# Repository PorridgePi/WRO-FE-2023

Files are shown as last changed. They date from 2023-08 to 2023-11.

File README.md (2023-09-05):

# WRO 2023 Future Engineers



# Team Information

Team ID: `FE0901`

Team Name: `raffles institution team 3`

Team Members
- [Yikun](https://github.com/PorridgePi)
- [Zachary](https://github.com/Zachareeeeee)

# Overview

Welcome to the GitHub repository for Team `FE0901` participating in WRO 2023. In this competition, we are building an autonomous robotic vehicle capable of completing 2 different challenges. This README provides a simple overview. If you wish to delve deeper into our engineering process, please check out our [Engineering Journal](docs/Engineering%20Journal.md) or [download it as PDF](https://github.com/PorridgePi/WRO-FE-2023/blob/main/docs/Engineering%20Journal.pdf).

## Demo

A demonstration video of our robot in action can be found on YouTube (or in the [video.md](video/video.md) file): [https://youtu.be/pbWbQL5pThI](https://youtu.be/pbWbQL5pThI)

Watch the video (https://www.youtube.com/embed/pbWbQL5pThI)

### Key Timestamps
Open Challenge
- Run 1: [00:03](https://youtu.be/pbWbQL5pThI&t=3)
- Runs 2 & 3: [01:15](https://youtu.be/pbWbQL5pThI&t=75)

Obstacle Challenge:
- Run 1: [03:40](https://youtu.be/pbWbQL5pThI&t=221)

# Usage
For Code, Using Visual Studio Code:
- Clone this repository: `git clone https://github.com/PorridgePi/WRO-FE-2023`
- Change directory: `cd ./WRO-FE-2023/`
- Initialise Git submodule(s): `git submodule update --init --recursive`
- Open the repository in VSCode: `code ./`
- Install the PlatformIO plugin
- Select the appropriate PlatformIO Environment
- Use the PlatformIO plugin to compile and upload code onto the microcontroller (Raspberry PI Pico)

For Camera (OpenMV): Using the [OpenMV IDE](https://openmv.io/pages/download)
- Open the camera code (`src/omv_main.py`) in OpenMV IDE
- Upload code onto OpenMV by:
    - Select `Tools` Menu
    - Click `Save open script onto OpenMV Cam (as main.py)`

For Documentation, Using [Obsidian](https://obsidian.md/):
- Clone this repository: `git clone https://github.com/PorridgePi/WRO-FE-2023`
- Open the cloned directory as a Vault

For PCB, Using [KiCAD](https://www.kicad.org/):
- Clone this repository: `git clone https://github.com/PorridgePi/WRO-FE-2023`
- Open the file `schemes/WRO_2023/WRO_2023.kicad_pro`

# Repository Content
- `.github/workflows/platformio-ci.yml`: GitHub Actions CI workflow for PlatformIO ([Documentation](https://docs.platformio.org/en/latest/integration/ci/github-actions.html))
- `.vscode/`: Folder containing VSCode workspace settings
    - `extensions.json`: List of recommended and unwanted extensions ([Documentation](https://code.visualstudio.com/docs/editor/extension-gallery#_workspace-recommended-extensions))
- `models/`: 3D models
- `others/`: Other files
- `schemes/`: Schematic diagram and PCB
    - `WRO_2023`: PCB files that can be opened in KiCAD
- `scripts/`: Scripts for PlatformIO
    - `ci.sh`: Script for CI test
- `src/`: Main code
    - `lib/`: Libraries for components
        - Notably:
            - `lib/private/Common.h`: Shared code between `open.cpp` and `obstacle.cpp`
            - `lib/Mecha_QMC5883L`: [Forked version](https://github.com/PorridgePi/Mecha_QMC5883L) of library for the QMC5883L magnetometer
    - `test/`: Test code
    - `main.cpp`: Placeholder file
    - `obstacle.cpp`: Code for the Obstacle Challenge
    - `open.cpp`: Code for the Open Challenge
- `t-photos`: Team photo
- `v-photos`: Photos of the vehicle (from many different angles!)
- `video`: Contains [video.md](video/video.md) with the link to the video of the driving demonstration
- `.clang-format`: ClangFormat code style file - to format code in VSCode
- `.gitignore`: gitignore file ([Documentation](https://git-scm.com/docs/gitignore))
- `platformio.ini`: PlatformIO configuration file ([Documentation](https://docs.platformio.org/en/stable/projectconf/index.html))
- `README.md`: This file

# Reminders before Running
1. Calibrate compass(es)
2. Ensure steering mechanism is tightened
3. Clean wheels to ensure grip

# Hardware used
- **Motor:** 1x GM25-12CPR 
- **Servo:** 1x MG996R
- **Motor Driver:** 1x AT8236
- **Microcontroller:** 1x Raspberry Pi Pico
- **Voltage Regulator (5V):** 1x CKCS-BK-2
- **LiDAR:** 5x TF-Luna
- **Camera:** 1x OpenMV M7
- **Compass:** 1x GY-273 and 1x GY-271
- **Battery:** 1x Turnigy nano-tech 1300mAh 3S 45~90C Lipo Pack

# Continual Integration (CI) Testing

We have a simple CI testing setup with GitHub Actions, using the `scripts/ci.sh` script to automate the process of building our code for all different environments in `platformio.ini`. It checks for build success and ensures that the code can be successfully compiled.

CI is a critical aspect of our development process. It allows us to detect issues and errors in our codebase as soon as they occur. This early detection is invaluable in preventing the accumulation of errors and simplifying debugging.

Besides, our project involves multiple team members working collaboratively. CI ensures that all code changes made by different team members do not introduce regressions or break existing functionality.

To check the status of our CI, go to the [`Actions` tab](https://github.com/PorridgePi/WRO-FE-2023/actions) and view the workflow runs. If everything is going well, you should be only seeing green ticks. However, if you are seeing red crosses, something is up, but don't fret, we are definitely working hard to iron out the bugs!

(or alternatively, just look at the badge below for the CI status)



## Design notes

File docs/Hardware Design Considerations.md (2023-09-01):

# Wheels
- Wide v.s. Thin
    - affect surface area in contact with ground, affecting how rubber gets squished
- Size (i.e. diameter) affects
    - size of cavity to allow steering
    - torque
        - larger the diameter, moment of inertia is higher, more torque required
    - distance travelled per revolution
- Mass

# Motor
- Encoder
- Motor Stall Current
    - proportional to Vin
- nominal voltage
- [Pulling power from the balance plug - RC Groups - https://www.rcgroups.com/forums/showthread.php?1442019-Pulling-power-from-the-balance-plug](https://www.rcgroups.com/forums/showthread.php?1442019-Pulling-power-from-the-balance-plug)
# Steering
- Take note of steer radius
    - tightest turn at corners would be less than 40cm (i.e. both blocks require keeping to the left)
    - movement between blocks would be around a maximum turn radius of 50cm
- Servo
    - [Servo - writeMicroseconds() - Arduino Reference - https://reference.arduino.cc/reference/en/libraries/servo/writemicroseconds/](https://reference.arduino.cc/reference/en/libraries/servo/writemicroseconds/)
    - use this instead of `.write()`
- [Servo Motors - Arduino - Wiki.nus - https://wiki.nus.edu.sg/display/Arduino/Servo+Motors](https://wiki.nus.edu.sg/display/Arduino/Servo+Motors)

    - need to take into account the length and width of the vehicle
    - lines from both front wheels and the line through back wheels should all come together at a single point
        - 
        - Tech Explained: Ackermann Steering Geometry - Racecar Engineering

- Website: [Ackerman Steering](http://datagenetics.com/blog/december12016/index.html)

# Ranging/Localisation
- LiDAR
- Camera
- Optical Flow

# Orientation
- IMU
- Compass

# Notes
- Ideally only camera for SLAM would yield the smallest robot

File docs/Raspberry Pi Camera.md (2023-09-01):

w- on [[2023-04-26]], checked out:
    - [Raspberry Pi and PiCam setup (headless)](https://gist.github.com/sageworksstudio/b0954d2d6cfac7d4a00e776953324a2c)
    - [Connect the Camera Module | Getting started with the Camera Module](https://projects.raspberrypi.org/en/projects/getting-started-with-picamera/2)
- [[2023-05-03]]
    - Issue:
        - `vcgencmd get_camera`: `supported=1 detected=1, libcamera interfaces=0`
        - but `libcamera-hello`: `ERROR: *** no cameras available ***`
    - Fix:
        - [Raspberry Pi Documentation - Camera software](https://www.raspberrypi.com/documentation/computers/camera_software.html)
            - > On Raspberry Pi 3 and earlier devices running Bullseye you need to re-enable Glamor in order to make the X-Windows hardware accelerated preview window work. To do this enter sudo raspi-config at a terminal window and then choose Advanced Options, Glamor and Yes. Finally quit raspi-config and let it reboot your Raspberry Pi.
            - > Raspberry Pi 3 and older devices may not by default be using the correct display driver. Refer to the /boot/config.txt file and ensure that either dtoverlay=vc4-fkms-v3d or dtoverlay=vc4-kms-v3d is currently active. Please reboot if you needed to change this.
        - Original reference to
            - [libcamera-apps not working on RPi 3 Model B+ · Issue #125 · raspberrypi/libcamera-apps](https://github.com/raspberrypi/libcamera-apps/issues/125)
            - [Raspbeery (bullseye) && libcamera - Stack Overflow](https://stackoverflow.com/questions/71709549/raspbeery-bullseye-libcamera/71712175#71712175)
    - Usage: `libcamera-hello -t 0` for no timeout
- [[2023-05-08]]
```python
from picamera2 import Picamera2
picam2 = Picamera2()
print(picam2.sensor_modes)
```

```json
[{'format': SRGGB10_CSI2P, 'unpacked': 'SRGGB10', 'bit_depth': 10, 'size': (640, 480), 'fps': 103.33, 'crop_limits': (1000, 752, 1280, 960), 'exposure_limits': (75, 11766829, None)}, {'format': SRGGB10_CSI2P, 'unpacked': 'SRGGB10', 'bit_depth': 10, 'size': (1640, 1232), 'fps': 41.85, 'crop_limits': (0, 0, 3280, 2464), 'exposure_limits': (75, 11766829, None)}, {'format': SRGGB10_CSI2P, 'unpacked': 'SRGGB10', 'bit_depth': 10, 'size': (1920, 1080), 'fps': 47.57, 'crop_limits': (680, 692, 1920, 1080), 'exposure_limits': (75, 11766829, None)}, {'format': SRGGB10_CSI2P, 'unpacked': 'SRGGB10', 'bit_depth': 10, 'size': (3280, 2464), 'fps': 21.19, 'crop_limits': (0, 0, 3280, 2464), 'exposure_limits': (75, 11766829, None)}, {'format': SRGGB8, 'unpacked': 'SRGGB8', 'bit_depth': 8, 'size': (640, 480), 'fps': 103.33, 'crop_limits': (1000, 752, 1280, 960), 'exposure_limits': (75, 11766829, None)}, {'format': SRGGB8, 'unpacked': 'SRGGB8', 'bit_depth': 8, 'size': (1640, 1232), 'fps': 41.85, 'crop_limits': (0, 0, 3280, 2464), 'exposure_limits': (75, 11766829, None)}, {'format': SRGGB8, 'unpacked': 'SRGGB8', 'bit_depth': 8, 'size': (1920, 1080), 'fps': 47.57, 'crop_limits': (680, 692, 1920, 1080), 'exposure_limits': (75, 11766829, None)}, {'format': SRGGB8, 'unpacked': 'SRGGB8', 'bit_depth': 8, 'size': (3280, 2464), 'fps': 21.19, 'crop_limits': (0, 0, 3280, 2464), 'exposure_limits': (75, 11766829, None)}]
>>> print(picam2.sensor_modes)
[{'format': SRGGB10_CSI2P, 'unpacked': 'SRGGB10', 'bit_depth': 10, 'size': (640, 480), 'fps': 103.33, 'crop_limits': (1000, 752, 1280, 960), 'exposure_limits': (75, 11766829, None)}, {'format': SRGGB10_CSI2P, 'unpacked': 'SRGGB10', 'bit_depth': 10, 'size': (1640, 1232), 'fps': 41.85, 'crop_limits': (0, 0, 3280, 2464), 'exposure_limits': (75, 11766829, None)}, {'format': SRGGB10_CSI2P, 'unpacked': 'SRGGB10', 'bit_depth': 10, 'size': (1920, 1080), 'fps': 47.57, 'crop_limits': (680, 692, 1920, 1080), 'exposure_limits': (75, 11766829, None)}, {'format': SRGGB10_CSI2P, 'unpacked': 'SRGGB10', 'bit_depth': 10, 'size': (3280, 2464), 'fps': 21.19, 'crop_limits': (0, 0, 3280, 2464), 'exposure_limits': (75, 11766829, None)}, {'format': SRGGB8, 'unpacked': 'SRGGB8', 'bit_depth': 8, 'size': (640, 480), 'fps': 103.33, 'crop_limits': (1000, 752, 1280, 960), 'exposure_limits': (75, 11766829, None)}, {'format': SRGGB8, 'unpacked': 'SRGGB8', 'bit_depth': 8, 'size': (1640, 1232), 'fps': 41.85, 'crop_limits': (0, 0, 3280, 2464), 'exposure_limits': (75, 11766829, None)}, {'format': SRGGB8, 'unpacked': 'SRGGB8', 'bit_depth': 8, 'size': (1920, 1080), 'fps': 47.57, 'crop_limits': (680, 692, 1920, 1080), 'exposure_limits': (75, 11766829, None)}, {'format': SRGGB8, 'unpacked': 'SRGGB8', 'bit_depth': 8, 'size': (3280, 2464), 'fps': 21.19, 'crop_limits': (0, 0, 3280, 2464), 'exposure_limits': (75, 11766829, None)}]
```

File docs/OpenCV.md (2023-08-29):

- [[2023-05-03]]
    - with [[Raspberry Pi Camera]]
        - Optimisation
            - [prepkg/opencv-raspberrypi: Precompiled OpenCV 4.7.0 binaries for Raspberry Pi 3 & 4](https://github.com/prepkg/opencv-raspberrypi)
            - [Optimizing OpenCV on the Raspberry Pi - PyImageSearch](https://pyimagesearch.com/2017/10/09/optimizing-opencv-on-the-raspberry-pi/)
        - [Using the Raspberry Pi Camera on Bullseye OS and OpenCV | Technology Tutorials](https://toptechboy.com/using-the-raspberry-pi-camera-on-bullseye-os-and-opencv/)
            - `pip install opencv-python==4.6.0.66`
            ```python
            import cv2
            from picamera2 import Picamera2
            picam2 = Picamera2()
            picam2.preview_configuration.main.size = (1280,720)
            picam2.preview_configuration.main.format = "RGB888"
            picam2.preview_configuration.align()
            picam2.configure("preview")
            picam2.start()
            while True:
                im= picam2.capture_array()
                cv2.imshow("Camera", im)
                if cv2.waitKey(1)==ord('q'):
                    break
            cv2.destroyAllWindows()
            ```

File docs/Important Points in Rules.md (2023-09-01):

# Focus Areas
- CV + sensor fusion
- open-source hardware
- movement different from differential drive
- optimal strategies
- engineering journal
# Getting Started Guide
- https://world-robot-olympiad-association.github.io/future-engineers-gs/
# Team's Own Work
- Note: 3.7 It is not allowed to use a vehicle’s control program that is (a.) the same or too similar to solutions sold online or (b.) the same or too similar to another solution at the competition and clearly not the own work of the team. This includes solutions from teams of the same institution and/or country. Since manufactured vehicles/sets can be used in the competition, the constructions of vehicles are not checked for plagiarism.
# Game Description
- One car per attempt will try to achieve the best time by driving several laps fully autonomously. The two challenges are the following:
    - Open Challenge: The vehicle must complete three (3) laps on the track with random placements of the inside track walls.
    - Obstacle Challenge: The vehicle must complete three (3) laps on the track with randomly placed green and red traffic signs. The traffic signs indicate the side of the lane the vehicle must follow. The traffic sign to keep to the right side of the lane is a red pillar. The traffic sign to keep to the left side of the lane is a green pillar. The continuation of the vehicle to the third round is indicated by the last traffic sign of the second round. A green traffic sign indicates that the robot must go ahead and continue the third round in the same direction. A red traffic sign indicates that the vehicle must turn around and complete the third round in the opposite direction. The vehicle is not allowed to move or knock down the traffic signs.

The starting direction in which the car must drive on the track (clockwise or counterclockwise) will vary in different challenge rounds. The starting position of the car as well as the number and location of traffic signs are randomly defined before the round (after the check time). The following graphic shows the game field with the game objects.

Straightforward Section
- 6 zones
- 4 T-intersections and 2 X-intersections
- traffic sign's seats
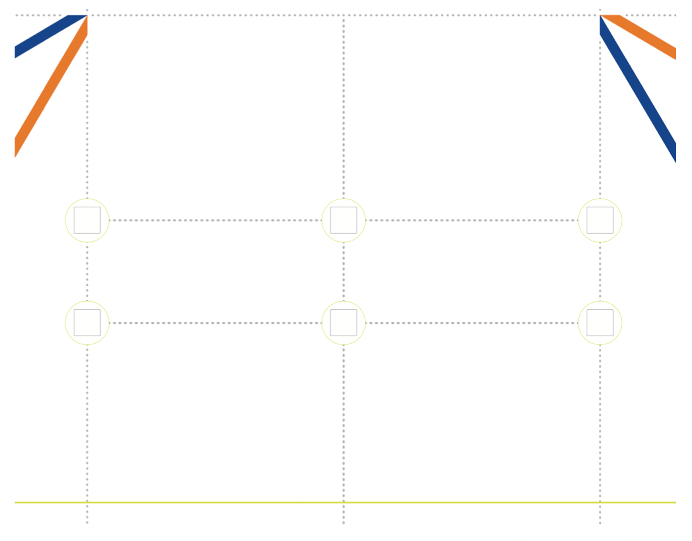
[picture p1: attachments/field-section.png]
    - 

# Engineer’s documentation on GitHub
documentation that presents their engineering progress, the final vehicle design and final vehicle source code

This documentation must be uploaded to the GitHub public repository, and a hardcopy must be submitted at the international final.

must provide the following:
-   Discussion, Information and motivation for the vehicle’s mobility, power and sense, and obstacle management.
    - sense - decision making
-   Photos of the vehicle (from every side, from top and bottom), and a team photo.
-   URL to YouTube (should be either public or accessible by link) showing the vehicle driving autonomously.
    - That part of the video where driving demonstration exists, must be at least 30 seconds in length.
    - One video for each challenge must be provided.
- Link to a GitHub public repository
    - with the code for all components which were programmed to participate in the competition
    - The repository may also include the files for models used by 3D printers, laser cutting machines and CNC machines to produce the vehicle elements.
    - The history of commits should contain at least 3 commits
        - the first one not later than 2 months before the competition – it must contain not less than 1/5 of the final amount of the code
        - The second one is not later than 1 month before the competition
        - the third one not later than 1 week before the competition.
    - The repository must contain a README.md file with a short description in English (not less than 5000 characters) of the designed solution.
    - The goal of the description is to clarify
        - which modules the code consists of
        - how they are related to the electromechanical components of the vehicle
        - and what is the process to build/compile/upload the code to the vehicle’s controllers
            - "Usage" section
    - A template for the GitHub repos is available on https://github.com/World-Robot-Olympiad-Association/wro2022-fe-template.

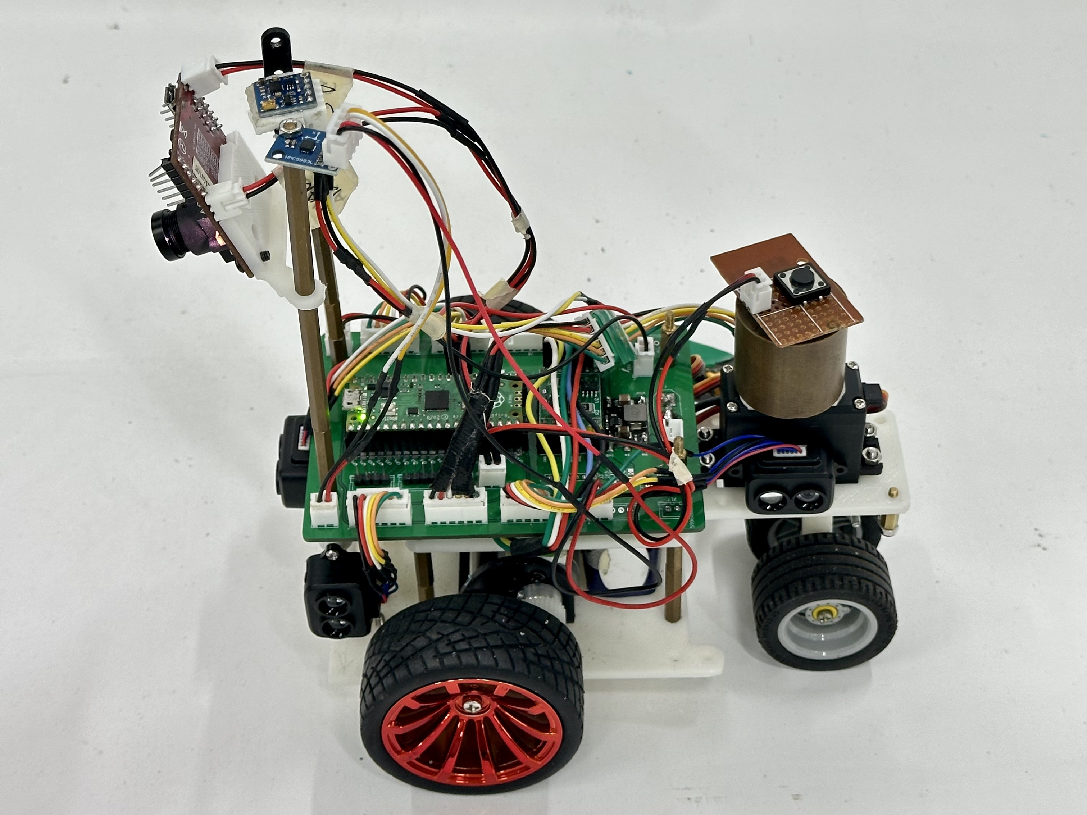
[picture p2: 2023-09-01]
v-photos/FE0901_Vehicle_Top_Left.jpeg

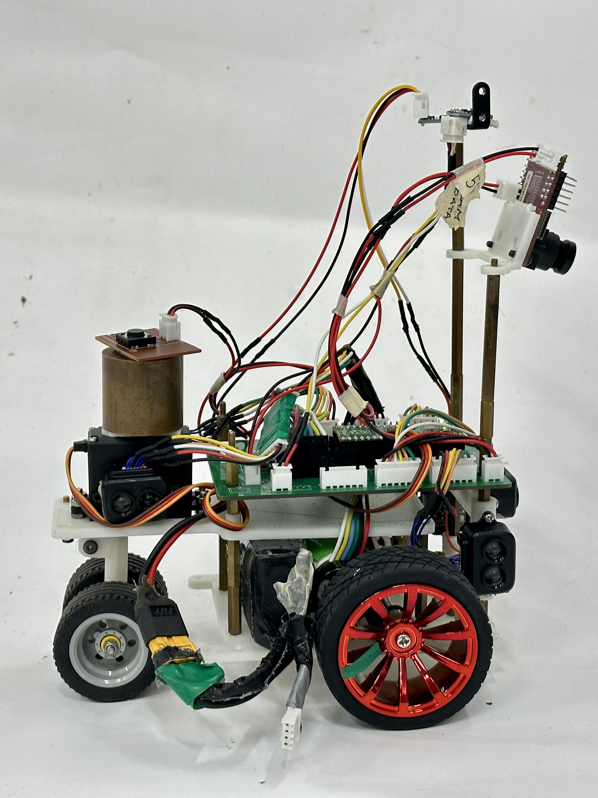
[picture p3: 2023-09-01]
v-photos/FE0901_Vehicle_Right.jpeg

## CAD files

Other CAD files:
models/bot.f3d

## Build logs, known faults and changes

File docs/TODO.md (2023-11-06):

- [ ] Things to pack
    - [ ] M3, M2 Screwsw
    - [x] Backup prints (especially steering column(
    - [ ] 3x TFLunas + Cables
    - [ ] 2x IMUs + Cables
    - [x] Spare Servo
    - [x] Spare Motor
    - [x] 2x Lego Wheels
    - [x] Mounting Tape
    - [ ] 4x Lipos (Total)
    - [ ] Spare (soldered) PCB
    - [x] Spare OpenMV
    - [x] Hot glue gun
    - [ ] Soldering Iron + Solder
- [ ] Integrate block detection
- [ ] Print backup parts
- [x] Pack the yellow measuring tape at the end of the day (due 6 Sept, completed 5 Sept)
- [x] START DOCUMENTING EVERYTHING (completed 28 Aug)
- [x] Figure out how to mount a compass (away from the ferromagnetic stuff) (completed 28 Aug)
- [x] Try to get OpenMV working? (completed 28 Aug)
- [x] CAD pivoting mount for camera (completed 28 Aug)
- [x] Test and set lidar I²C addresses (completed 27 July)
- [x] Test steering servo and generate look up table for steering angles (completed 27 July)
- [x] Get materials for gamemat (completed 27 July)
- [x] CAD lidar mounts and start testing? (completed 20 July)

![[../attachments/Microsoft To Do Export.pdf]]

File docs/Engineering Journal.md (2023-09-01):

# Engineering Jounral

Team ID: `FE0901`

Team Name: `raffles institution team 3`

Team Members:
- Zhou Yikun
- Zachary Ang

# Contents
1. Hardware Overview
2. Mobility Management
3. Power and Sense
4. Obstacle Management
5. Code Style Guidelines

# Introduction

A copy of this Engineering Journal can also be found on [GitHub](https://github.com/PorridgePi/WRO-FE-2023/blob/main/docs/Engineering%20Journal.md).

Other notes that we took are also found in the `docs/` subdirectory.

# 1. Hardware Overview

## Bill of Materials (BOM)

| Description | Brand | Model | Number | Others | |
| --- | --- | --- | --- | --- | --- |
| Motor | YFROBOT | GM25-12CPR | 1 | Contains Encoder, [Link](https://yfrobot.com/products/metal-gearmotor-ga25-12v-with-16-cpr-encoder), , [Doc 1](https://files.seeedstudio.com/wiki/Skeleton_Bot-4WD_hercules_mobile_robotic_platform/res/Specifications_for_Motor.pdf), [Doc 2](https://osoyoo.com/picture/mecanum_wheel_robotic/GM25-370-motor%20specification.pdf) | |
| Servo | Tower-Pro | MG996R | 1 | [Schematics](https://www.electronicoscaldas.com/datasheet/MG996R_Tower-Pro.pdf) | |
| Motor Driver | - | AT8236 | 1 | | |
| Microcontroller | Raspberry Pi | Pico | 1 | | |
| Voltage Regulator | CKCS | CKCS-BK-2 | 1 | 5V4A Output | |
| LiDAR | - | TF-Luna | 5 | | |
| PCB | JLCPCB | - | 1 | | |
| Camera | OpenMV | M7 | 1 | | |
| Compass | - | GY-273 | 1 | Labelled HMC5883L, using QMC5883L | |
| Compass | - | GY-271 | 1 | Uses QMC5883L | |
| LiPo Battery | Turnigy | Nano-tech 1300mAh 3S 45~90C | | | | | |

## Components Wiring Diagram

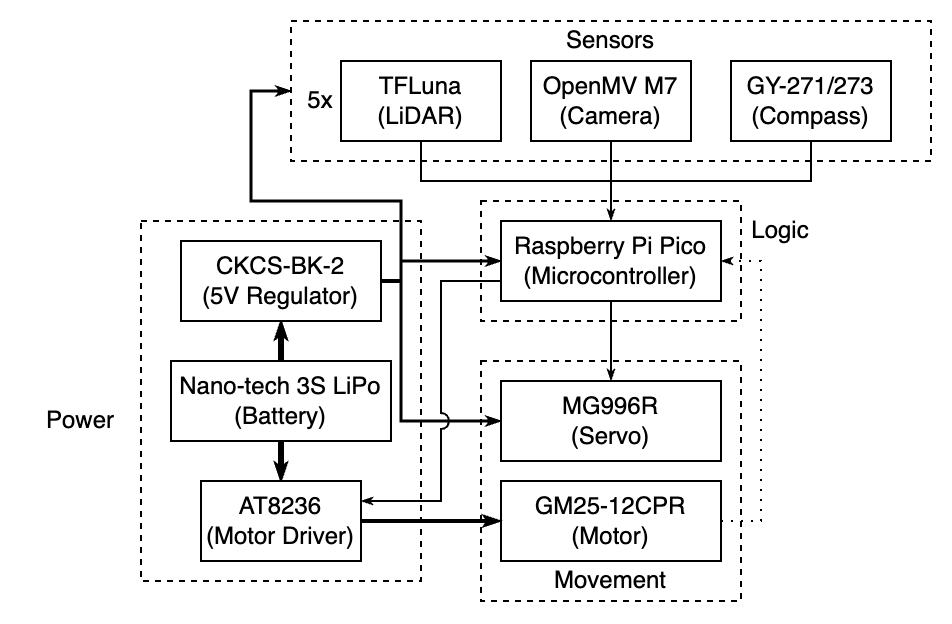
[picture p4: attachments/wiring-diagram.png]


# 2. Mobility Management

## Motor

The motor we used for propulsion was the GM25-12CPR. We chose it because we had a few leftover from other projects, and its speed and specifications appeared suitable for our current competition. While we initially considered other motor options, the availability of the GM25-12CPR made it a practical choice, allowing us to start working on the robot without delays. It was essential to have a motor in hand to begin the design and testing phases.

The motor is mounted to the vehicle using an included metal bracket, and placed lower down, along with other heavy components, to lower the centre of gravity of the robot, and hence improve stability.

The gearbox attached to the motor was mounted inline with the motor which reduced the vertical space taken up by the motor, at the expense of restricting the possible orientations in can be mounted.

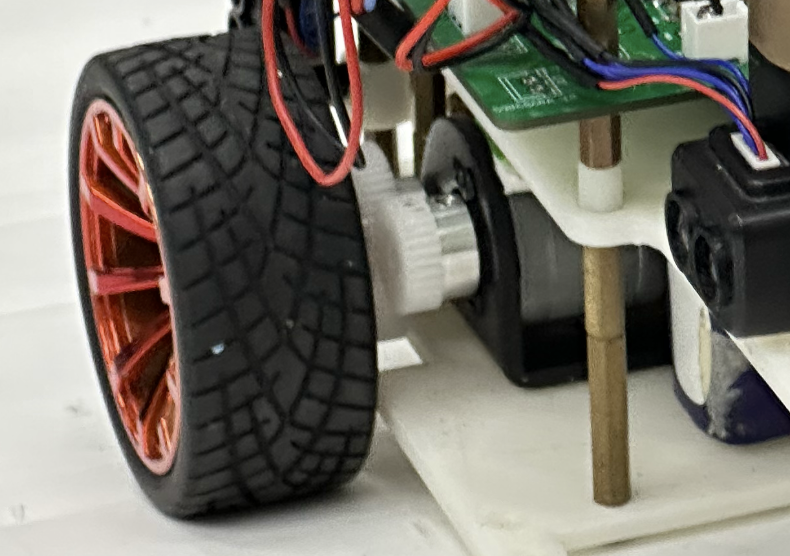
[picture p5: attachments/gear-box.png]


### Motor Driver

We purchased the motor before deciding on which motor driver to use to power the motor. Unbeknownst to us at that time, this was a bad idea. Instead, we should have decided on a motor driver, before finding a suitable motor.

After making the purchase for the motor, we started looking for a suitable motor driver. To do so, we have to find the maximum current which the motor would run at, which would be the stalling current. However, this is where the nightmare began. There was conflicting information for the motor, even from the same distributor (motor sold as a kit vs the motor alone had different specs). Then, generalising the search to the generic motor itself (the GM25-370), we discovered even more conflicting information.

In the end, we decided to take the highest stalling current that we could find on the internet, so that our motor driver would not just burn up immediately when the motor stalls. The value was 4A at 8.4V, and 6A at 12V.

Initially when the motor arrived, we tested it with a motor driver that we had on hand - the [SparkFun TB6612FNG](https://www.sparkfun.com/products/14451). It has a rated maximum sustained current of 1.2A per channel and a peak current of 3.2A per channel. The maximum sustained value was much lower than the supposed stall current of the motor, but the peak current seemed promisingly high to be used, so we continued with out test and thankfully, the driver did not burn up during out testing. We even researched and discovered that we could connect and join the two channel inputs and outputs together, to double the maximum sustained and peak current, literally. However, we decided to find a better alternative in mind of the (low but still present) possibility of the motor driver, a critical component, malfunctioning.

We prioritized finding a motor driver that could accommodate the potential higher stall current, which led us to the AT8236 motor driver with built-in overcurrent protection, and a maximum sustained and peak output current of 4A and 6A respectively. This was as high as our stall current could potentially be. This choice offered peace of mind and a safety net against unexpected current spikes.

Besides, for additional peace of mind, we designed the PCB in a way that would allow us to combine the two channels to achieve double current output, by simply connecting two solder pads on the PCB. Up til now, it seems that a single channel is more than sufficient for the motor and we have not needed to use the combined dual channel output.

## Steering - Servo

The vehicle has a single servo rotating the steering axle through a single shaft, as opposed to more conventional steering geometries with multiple linkages and pivots, cutting down on complexity.

The steering axle was designed to be as close as possible to the drive axle to minimise the turning radius, while allowing sufficient space for the steering wheels to rotate freely.
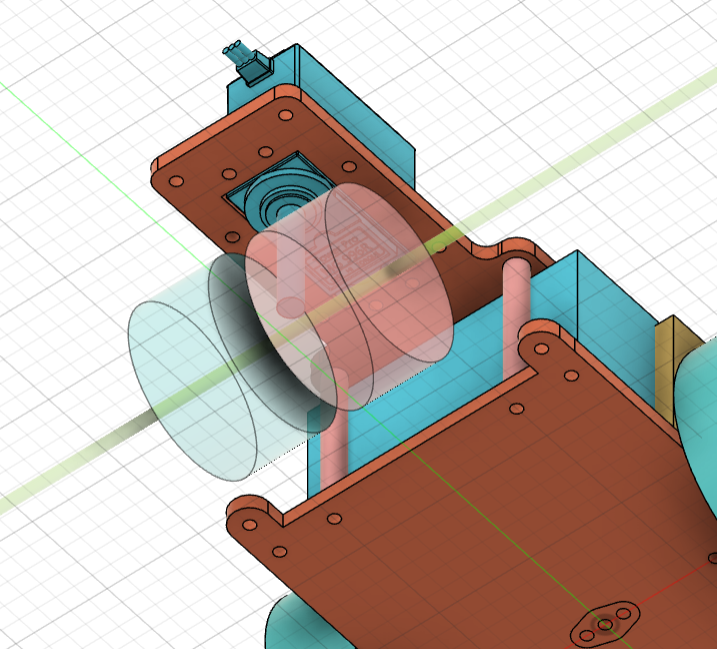
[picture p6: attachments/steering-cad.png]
   

Given that $\text{Turn radius} \approx D\tan({90\degree-\theta\degree})$, where $D$ is the distance between the steering and driving axle, and $\theta$ is the steering angle, minimising $D$ would be ideal. 

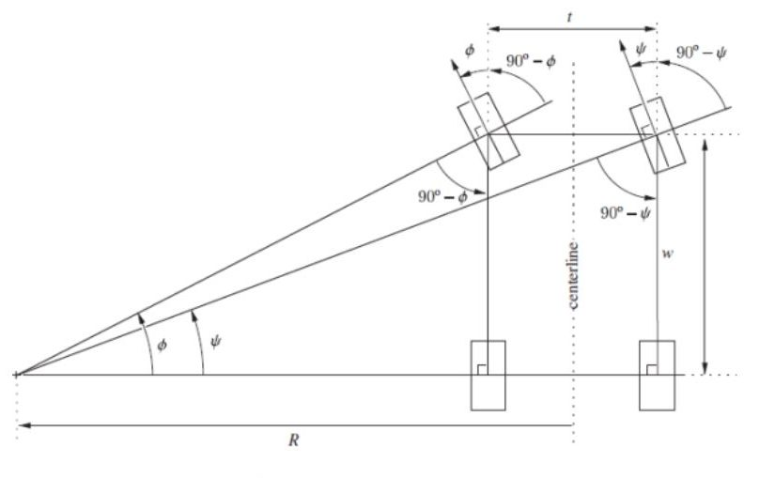
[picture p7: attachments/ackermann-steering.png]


## Vehicle Chassis Design

The chassis was designed to use articulated steering, which allowed for larger steering angles while keeping the steering mechanism relatively simple. 

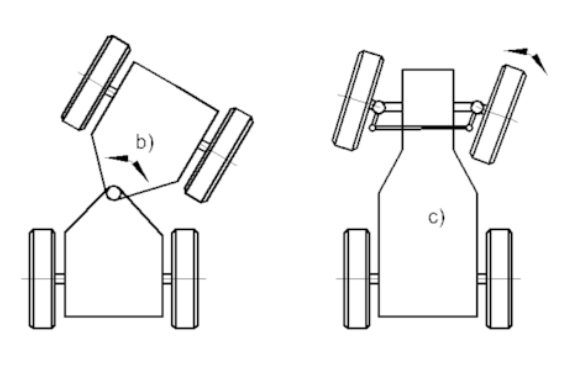
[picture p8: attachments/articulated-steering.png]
   

Above is an illustration of articulated steering on the left (b), and typical Ackermann steering on the right (c).

Our robot's design is articulated steering, just that one side of the steering does not have anything while the other has the rest of the components. In (b), it is showing the vehicle being split in the middle, but in our design, the vehicle is basically split at the servo and theres almost nothing on the other side.

Overall, we have standardised all holes to be M3 sized, so different components, including the baseplate, upper plate, and PCB, can be connected via M3 standoffs. This allowed for flexibility in adjusting the height, and made swapping components easier.

# 3. Power and Sense

## Power

Generally, there are 2 main voltages present on the PCB - 12V from the LiPo battery, and 5V that is stepped down from the 12V via a voltage regulator. 

In greater detail:
- 12V LiPo battery powers:
    - Motor driver to supply power to the single motor
    - Voltage regulator that outputs 5V with a maximum sustained current of 4A
- Resultant 5V from voltage regulator powers:
    - Sensors (LiDAR and Compass)
    - Microcontroller (Raspberry Pi Pico)
    - Camera (OpenMV M7)
    - Servo
    - Motor driver signal
    - Encoder on the motor

### Choice of LiPo batteries

- LiPo
    - suitable voltage - closest to most common voltage used by components
    - 18650 - 2x3.7V?
    - if really needed - check conversion efficiency of voltage regulator

## Communication

Various sensors, and the camera, communicate with the main microcontroller, Raspberry Pi Pico, via multiple protocols.

Inputs
- LiDAR: I2C
    - Each LiDAR is either set to a different I2C address, or run on a different I2C bus of the Pico
- Camera: UART
- Compass: I2C
    - One compass per I2C bus for failsafe
- Encoder: digital HIGH/LOW signals

Outputs
- Motor driver: PWM signal
- Servo: A form of PWM signal, using the Arduino `Servo` library

## Choice of Components

### Microcontroller

The Raspberry Pi Pico was chosen for various reasons:
- Affordability
    - Pico is extremely affordable, priced at 4.00 USD each, compared to alternatives like Arduino and Teensy MCUs which can cost easily upwards of tens of US dollars.
    - Hence, the Pico was cost-effective and aligned with our budget constraints. We aimed to strike a balance between performance and cost, and the Pico easily met our requirements without exceeding our budget.
- Fast processor and Memory
    - Pico has a dual-core Arm Cortex-M0+ processor that runs at 133 Mhz, which is much faster than alternatives like the Arduino Nano (16 Mhz). While it is slower than the Teensy 4.0 which runs at 400 Mhz, it has two cores instead of one, allowing for multicore operations. This is not to ignore the price advantage Pico has over alternatives.
        - With regards to the dual core processor, we actively took advantage of it, by running the movement control code (i.e. movement motor and steering via servo) on the second core while running the main loop gathering and processing data from sensors to make movement decisions on the main core.
- Variety of Protocols and GPIO Pins
    - GPIO pins on the Pico are multi-purpose, and each pin could be used with almost any supported protocol, including 2 x I2C buses, 2 x SPI buses, 2 UART ports, 16 x PWM channels and 3 x analog ports.
        - More interfaces available than alternatives such as the Arduino Nano and 
        - Such a multitude of protocols allow us to connect any peripherals such as sensors we want.
- Compatibility with Arduino
    - We are already familiar with the Arduino ecosystem, so finding a microcontroller that is compatible with Arduino is key
- Size
    - Despite Pico's small size, it still packs in a lot of capabilities

### Distance ranging sensor - LiDAR

LiDAR was chosen instead of alternative such as ultrasonic sensor due to its accuracy. Ultrasonic sensors, from past experience, have always been very unreliable, with values jumping around frequently, or even the entire sensor malfunctioning and causing the entire I2C bus to hang.

Besides, ultrasonic sensors may not work as well as LiDAR in this game field, where long distance ranging is required, and the field is huge (3m by 3m). Ultrasonic sensors also tend to interfere with each other, especially when we multiple need to be used simultaneously like in our case.

While the LiDAR readings may not be entirely foolproof, and are still subject to the reflectivity of the target object, they will suffice for our use.

Additionally, we had LiDAR sensors available on hand, and we have prior experience working with them, so it was a natural choice.

Initially, we were only intending on using 3 LiDARs - 2 facing left and right, and one facing forward - however we had issues with detecting corners and decided to install another pair of side facing LiDARs towards the rear. By comparing the reading from the 2 LiDARs, we were able to determine when a corner occured as the first LiDAR would no longer be detecting the wall while the rear LiDAR still was, fixing the corner detection issue.

The TFLunas used have a maximum range of 2m which is sufficient for detecting the side walls but may at times not have enough especially for the front facing LiDAR.

### Battery

The vehicle is powered off a single 3-cell Lithium Polymer (LiPo) battery, which allows for high peak current draw in excess of 10A.

While we considered using 18650 batteries, since 12V was unnecessary, we ultimately decided against it.

We invested in a carrier board while testing the 18650s but it increased the footprint of the batteries and lacked the convenience of a simple XT60 connector, making swapping batteries harder. On top of that, the 2A overcurrent protection severely limited the hardware we could use.

On the other hand, we had many LiPos, was capable of handling plenty of current, and were rectangular, which made designing the bot around them much easier.

### Camera

After some initial research, we shortlisted 3 main choices for a camera.

1. PixyCam
2. Raspberry Pi Camera with OpenCV
3. OpenMV

#### PixyCam

We had used PixyCams before but did not enjoy the lack of ability to write your own image processing algorithms. Sometimes the inbuilt algorithm simply could not recognise the colour you pick out via the UI, and you cannot do anything about it but to try and select the colour again.

Hence, we eliminated the PixyCam as a possibility.

#### Raspberry Pi Camera

We also considered using a Raspberry Pi Camera Module, but after some trial and error, our inexperience with writing code in OpenCV, as well as the difficulties in setting up a fully functional OpenCV environment on a full-fledged Linux distribution led us to our final decision against using it.

#### OpenMV

Finally, we arrived at our choice - the OpenMV M7. We had several of them on hand, and could start testing it immediately.

Compared to the power-hungry OpenCV, OpenMV is highly optimised for efficiency, thus reducing latency which is key in robotics competitions. Besides, OpenMV is tightly integrated with the OpenMV camera hardware, and provides a simplified interface in the form of the OpenMV IDE, which was way easier to use than setting up OpenCV from scratch on the Raspberry Pi.

We eventually settled on mounting an OpenMV M7 on the front of the vehicle, pointing slightly downwards to increase the field of view below the camera.

On a side note, we did consider dual/stereo cameras, and try out Simultaneous Localisation and Mapping (SLAM), but eventually decided not to due to its complexity.

### PCB

While prototyping, we realised that we require the use of many sensors. We initially used bread boards to connect the microcontroller to the peripherals. We realised that connecting them via jumper wires would not be reliable. An alternative was to solder by hand using protoboards, but that would take too much time.

In the end, we decided to design and make a PCB, since manufacturing nowadays, with JLCPCB available, was cheap and quick.

Here are some renders of the PCB.

Front:

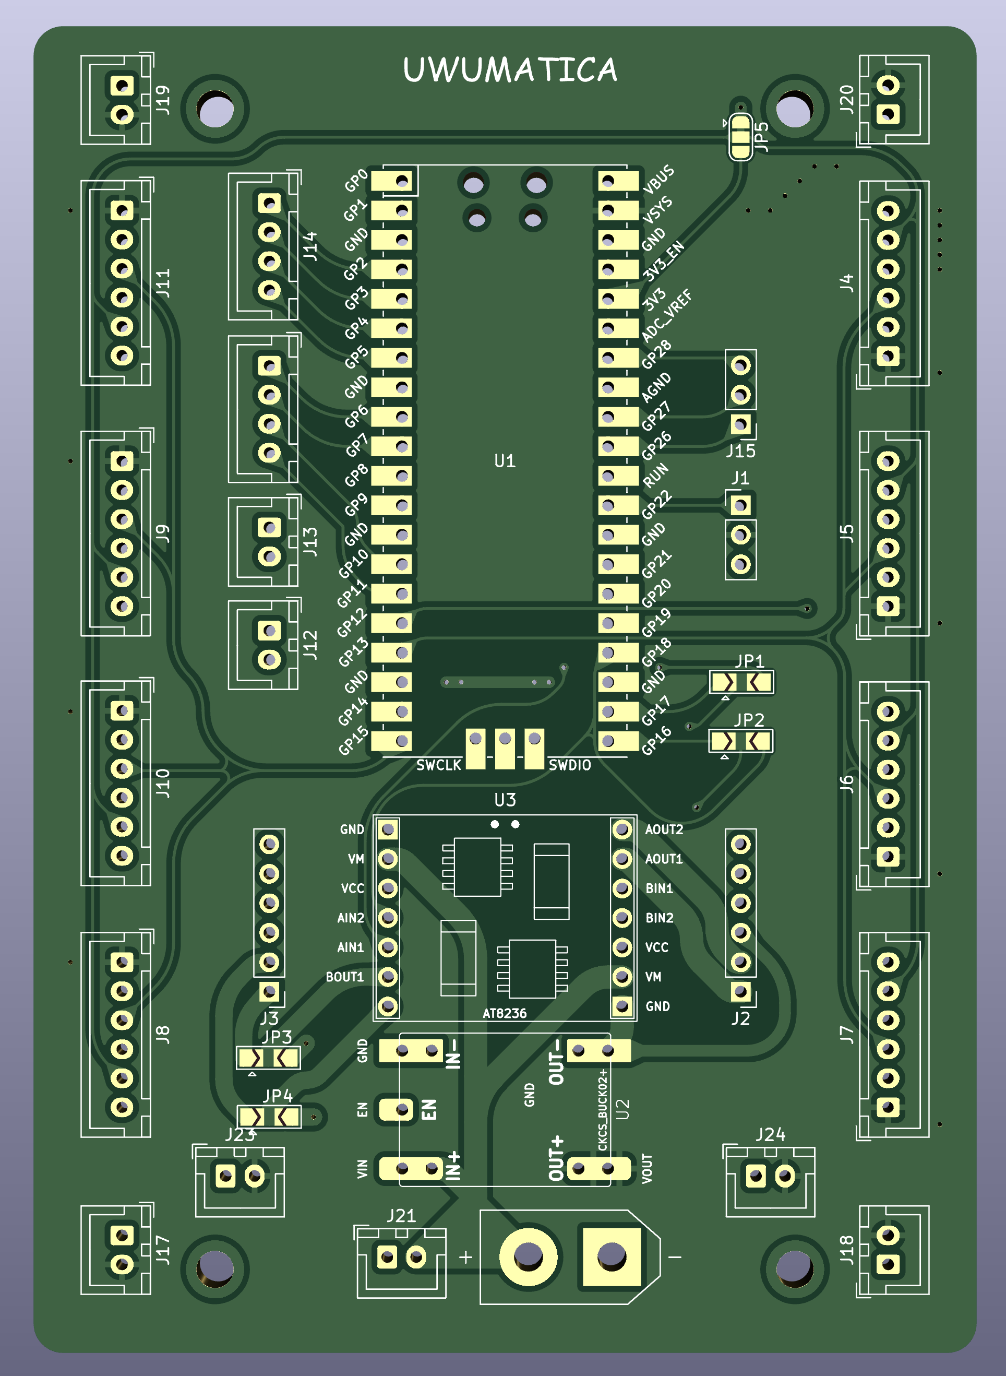
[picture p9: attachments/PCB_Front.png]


Back:

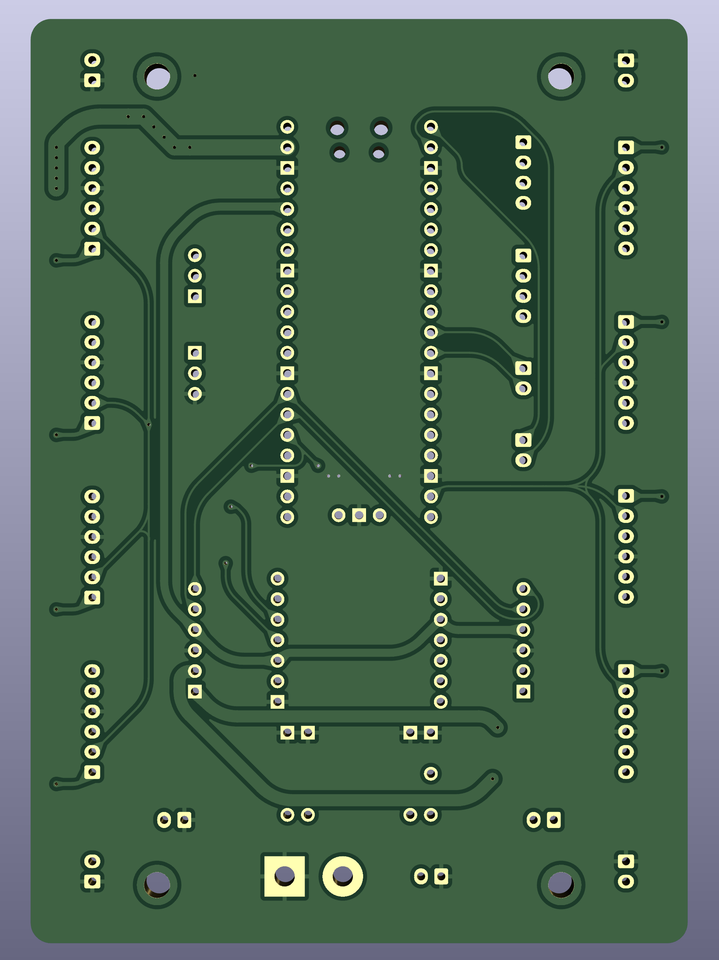
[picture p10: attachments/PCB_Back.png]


Below is the schematics for the PCB. (A full image is available on GitHub too under `schemes/`)

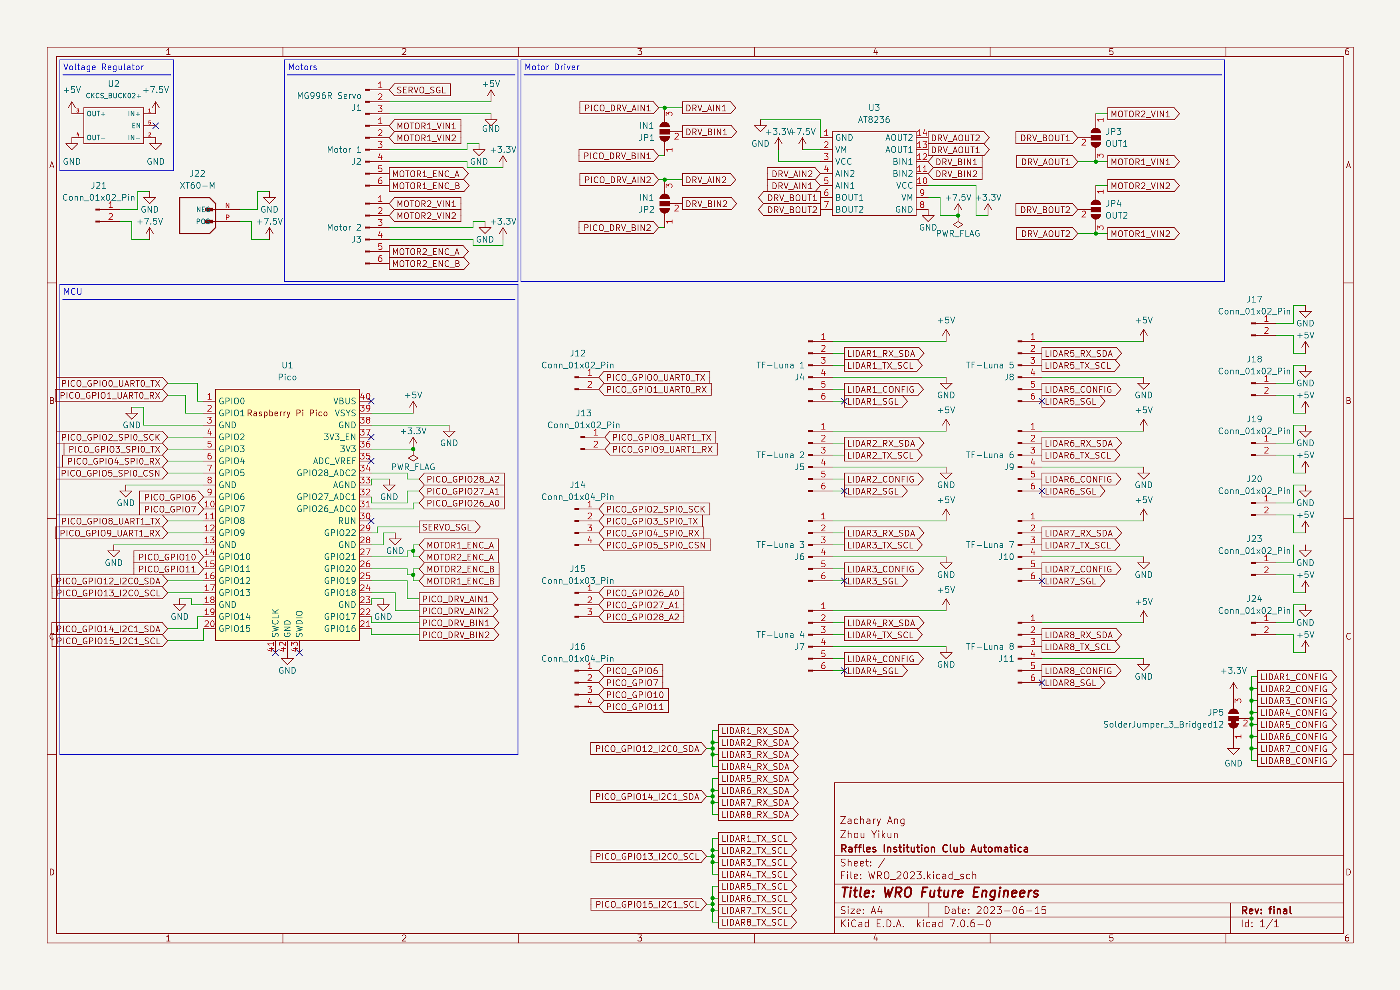
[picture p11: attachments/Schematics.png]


# 4. Obstacle management

## Open Challenge

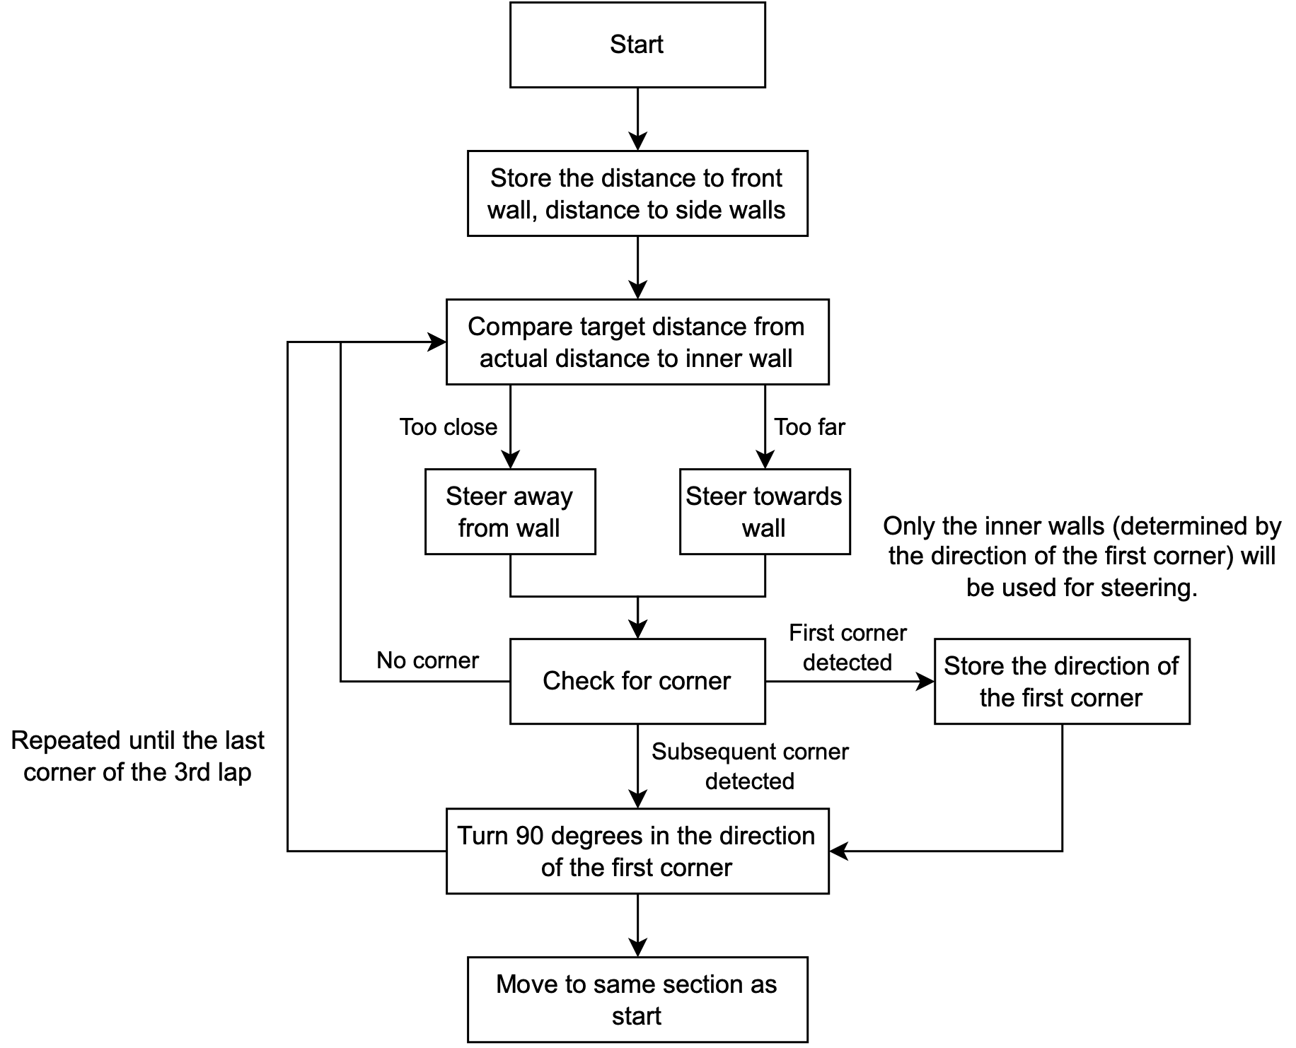
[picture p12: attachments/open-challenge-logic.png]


1. For the open round, the vehicle attempts to maintain a fixed distance from the inner wall. 2 LiDARs, mounted at the front and rear of the vehicle, face the inner wall and are used to gauge the vehicle's proximity and angle with respect to the wall. Corners are detected based on the disparity between the 2 LiDAR readings with the LiDARs, with the forward LiDARs detecting the sudden increase in range before the rear LiDARs.
2. When the vehicle is started, it measures the range to the front and sides to get its start position, which is used to determine its starting section.

## Obstacle Challenge

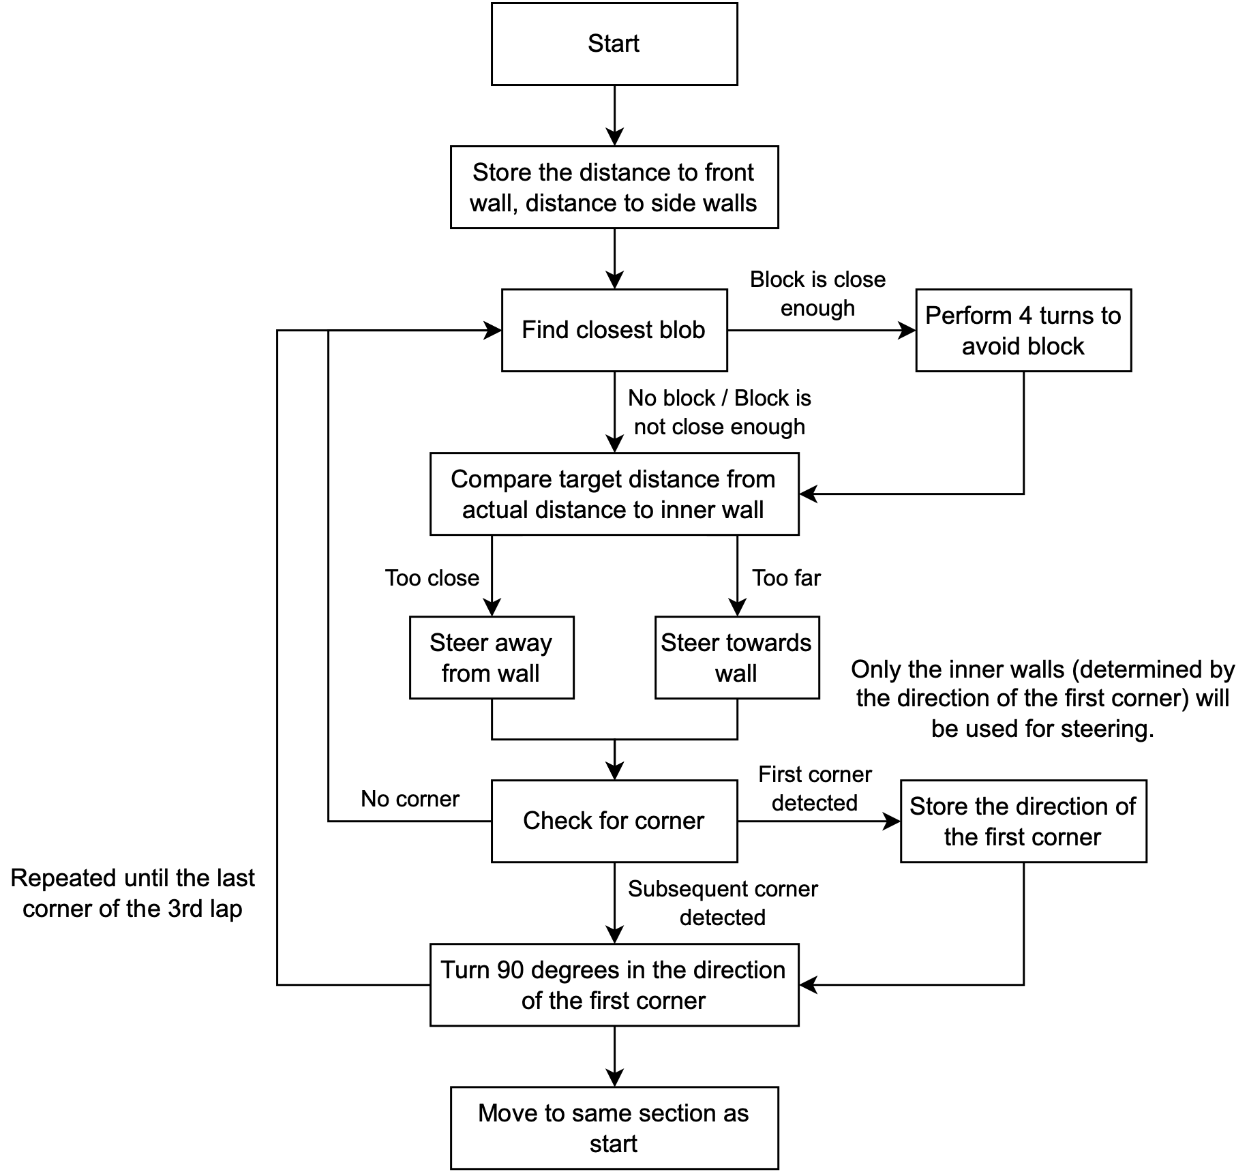
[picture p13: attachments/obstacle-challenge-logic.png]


1. For the obstacle round, blocks were detected using the blob identification library that came with the OpenMV software.
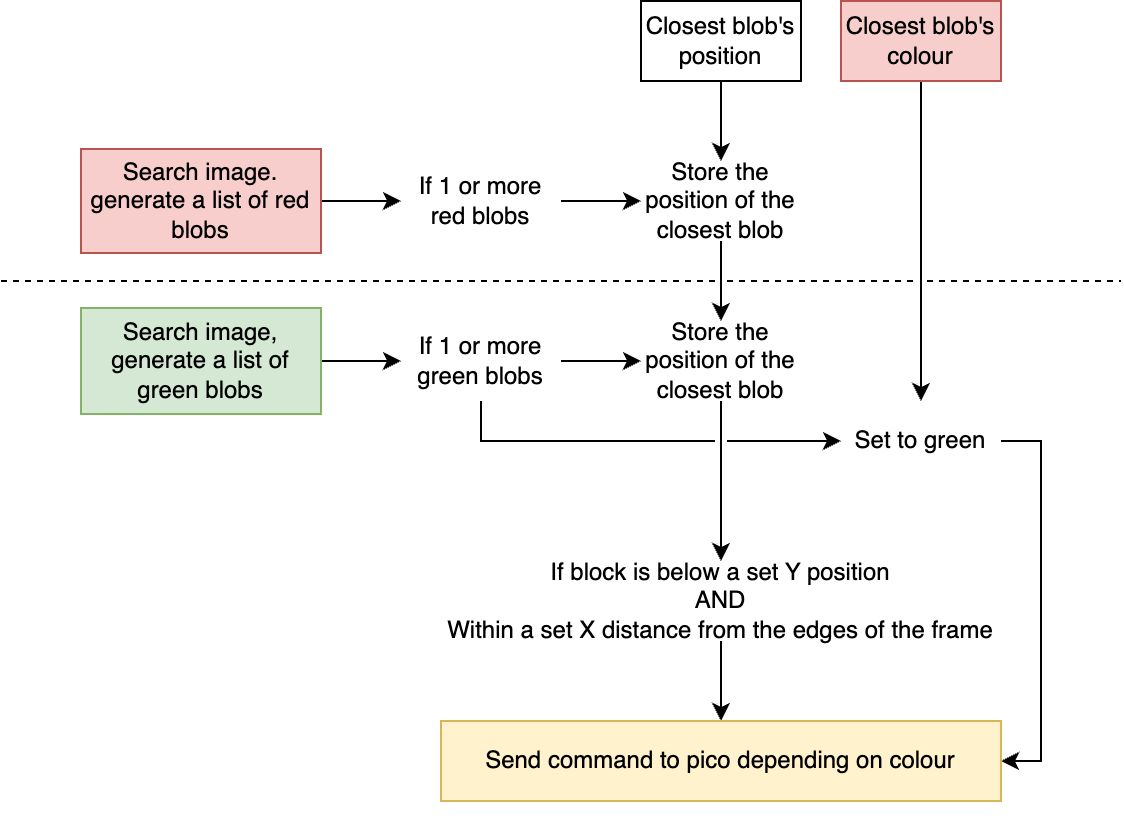
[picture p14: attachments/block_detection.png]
   
2. The all the green and red blobs are compared and the block whose centroid lies the lowest in the camera's frame is used as the closest block.
3. Once the closest block falls below a preset Y threshold, the OpenMV sends a command the the Pico. The Pico then performs 4 turns to evade the block and afterwards, return to the initial path.
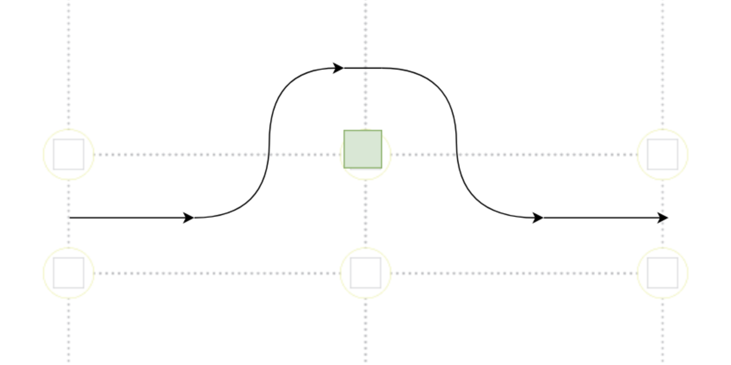
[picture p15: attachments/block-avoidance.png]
   

# 5. Code Style Guidelines

From the beginning, we decided to come up with a set of code style guidelines to follow, so as to help maintain consistency in our code, and to ensure the code is readable and maintainable, which is especially important as we work on complex autonomous robot systems.

The guidelines are:
- Annotate code where possible.
- Delete unused code unless intended for immediate use.
- Avoid long equations, ie. break them down into a few statements.
- Naming:
    - `PascalCase` for class names.
    - `camelCase` for normal variable names.
    - `UPPER_SNAKE_CASE` for definitions or constants.
    - Capitalise acronyms.
- Object-oriented programming (with the use of libraries and classes)

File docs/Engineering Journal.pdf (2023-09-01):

Engineering Jounral

Team ID: FE0901

Team Name: raffles institution team 3

Team Members:

Zhou Yikun
Zachary Ang

Contents

1. Hardware Overview
2. Mobility Management
3. Power and Sense
4. Obstacle Management
5. Code Style Guidelines

Introduction

A copy of this Engineering Journal can also be found on GitHub. (https://github.com/PorridgePi/WRO-FE-2023/blob/main/docs/Engineering%20Journal.md)

Other notes that we took are also found in the docs/ subdirectory.

1. Hardware Overview

Bill of Materials (BOM)

Description | Brand | Model | Number | Others
Motor | YFROBOT | GM25-12CPR | 1 | Contains Encoder, Link, (https://yfrobot.com/products/metal-gearmotor-ga25-12v-with-16-cpr-encoder) , Doc 1, (https://files.seeedstudio.com/wiki/Skeleton_Bot-4WD_hercules_mobile_robotic_platform/res/Specifications_for_Motor.pdf) Doc 2 (https://osoyoo.com/picture/mecanum_wheel_robotic/GM25-370-motor%20specification.pdf)
Servo | Tower-Pro | MG996R | 1 | Schematics (https://www.electronicoscaldas.com/datasheet/MG996R_Tower-Pro.pdf)
Motor Driver | - | AT8236 | 1
Microcontroller | Raspberry Pi | Pico | 1
Voltage Regulator | CKCS | CKCS-BK-2 | 1 | 5V4A Output
LiDAR | - | TF-Luna | 5
PCB | JLCPCB | - | 1
Camera | OpenMV | M7 | 1
Compass | - | GY-273 | 1 | Labelled HMC5883L, using QMC5883L
Compass | - | GY-271 | 1 | Uses QMC5883L
LiPo Battery | Turnigy | Nano-tech 1300mAh 3S 45~90C

Components Wiring Diagram

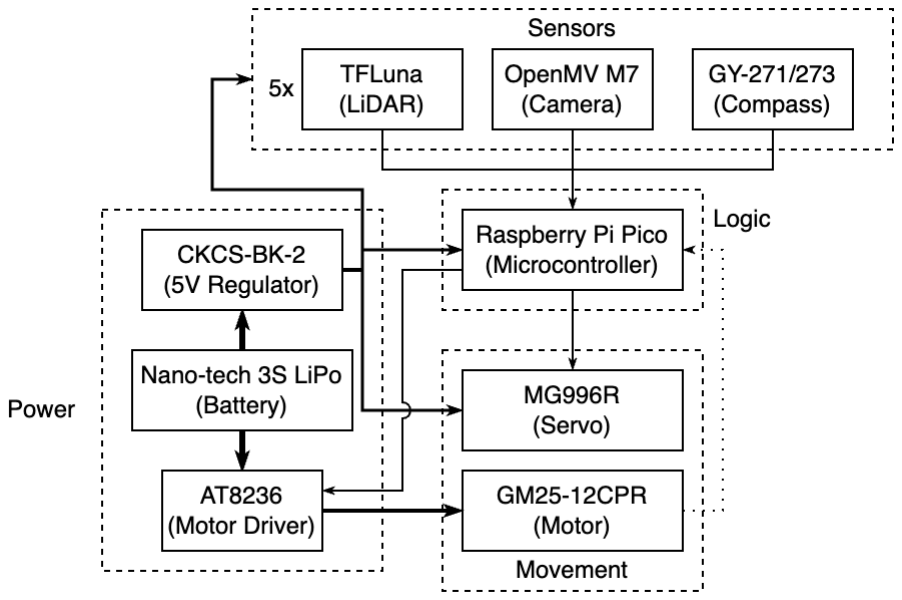
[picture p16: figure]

2. Mobility Management

Motor

The motor we used for propulsion was the GM25-12CPR. We chose it because we had a few leftover from other projects, and its speed and specifications appeared suitable for our current competition. While we initially considered other motor options, the availability of the GM25-12CPR made it a practical choice, allowing us to start working on the robot without delays. It was essential to have a motor in hand to begin the design and testing phases.

The motor is mounted to the vehicle using an included metal bracket, and placed lower down, along with other heavy components, to lower the centre of gravity of the robot, and hence improve stability.

The gearbox attached to the motor was mounted inline with the motor which reduced the vertical space taken up by the motor, at the expense of restricting the possible orientations in can be mounted.


Motor Driver

We purchased the motor before deciding on which motor driver to use to power the motor. Unbeknownst to us at that time, this was a bad idea. Instead, we should have decided on a motor driver, before finding a suitable motor.

After making the purchase for the motor, we started looking for a suitable motor driver. To do so, we have to find the maximum current which the motor would run at, which would be the stalling current. However, this is where the nightmare began. There was conflicting information for the motor, even from the same distributor (motor sold as a kit vs the motor alone had different specs). Then, generalising the search to the generic motor itself (the GM25-370), we discovered even more conflicting information.

In the end, we decided to take the highest stalling current that we could find on the internet, so that our motor driver would not just burn up immediately when the motor stalls. The value was 4A at 8.4V, and 6A at 12V.

Initially when the motor arrived, we tested it with a motor driver that we had on hand -the SparkFun TB6612FNG. (https://www.sparkfun.com/products/14451) It has a rated maximum sustained current of 1.2A per channel and a peak current of 3.2A per channel. The maximum sustained value was much lower than the supposed stall current of the motor, but the peak current seemed promisingly high to be used, so we continued with out test and thankfully, the driver did not burn up during out testing. We even researched and discovered that we could connect and join the two channel inputs and outputs together, to double the maximum sustained and peak current, literally. However, we decided to find a better alternative in mind of the (low but still present) possibility of the motor driver, a critical component, malfunctioning.

We prioritized finding a motor driver that could accommodate the potential higher stall current, which led us to the AT8236 motor driver with built-in overcurrent protection, and a maximum sustained and peak output current of 4A and 6A respectively. This was as high as our stall current could potentially be. This choice offered peace of mind and a safety net against unexpected current spikes.

Besides, for additional peace of mind, we designed the PCB in a way that would allow us to combine the two channels to achieve double current output, by simply connecting two solder pads on the PCB. Up til now, it seems that a single channel is more than sufficient for the motor and we have not needed to use the combined dual channel output.

Steering - Servo

The vehicle has a single servo rotating the steering axle through a single shaft, as opposed to more conventional steering geometries with multiple linkages and pivots, cutting down on complexity.

The steering axle was designed to be as close as possible to the drive axle to minimise the turning radius, while allowing sufficient space for the steering wheels to rotate freely.


Given that Turn radius ≈ D tan(90° − θ°), where D is the distance between the steering and driving axle, and θ is the steering angle, minimising D would be ideal.

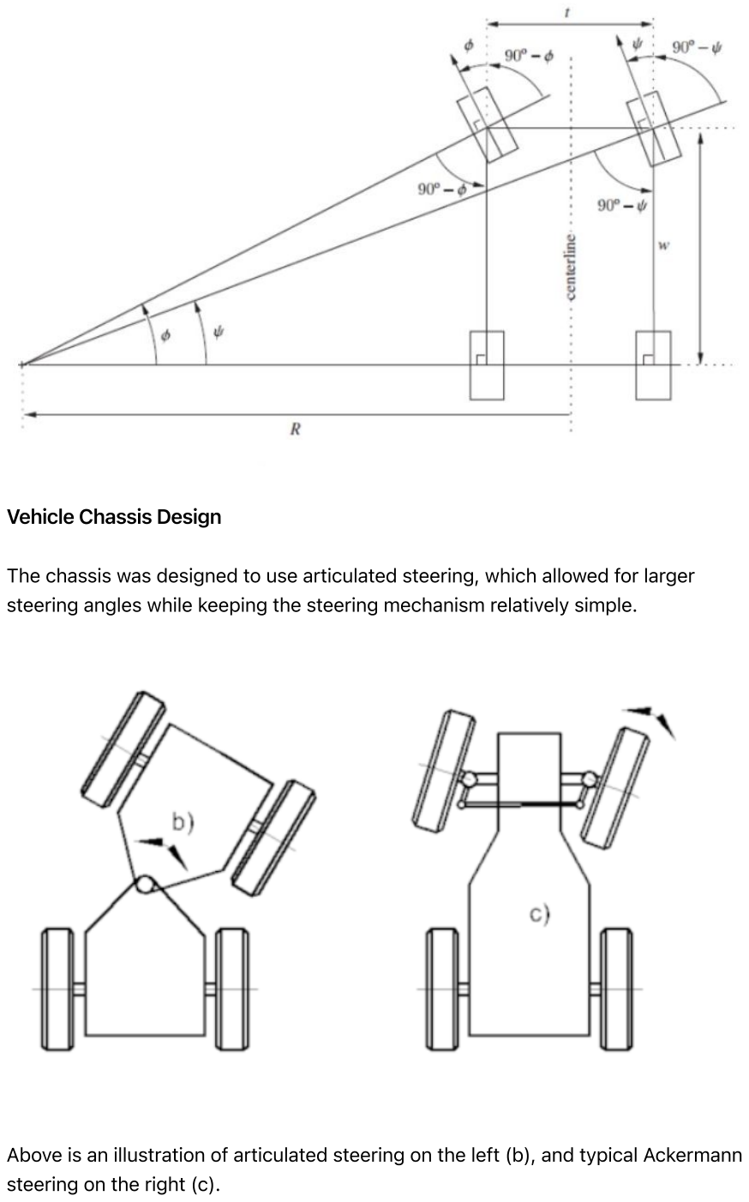
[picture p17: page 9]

Vehicle Chassis Design

The chassis was designed to use articulated steering, which allowed for larger steering angles while keeping the steering mechanism relatively simple.

Above is an illustration of articulated steering on the left (b), and typical Ackermann steering on the right (c).

Our robot's design is articulated steering, just that one side of the steering does not have anything while the other has the rest of the components. In (b), it is showing the vehicle being split in the middle, but in our design, the vehicle is basically split at the servo and theres almost nothing on the other side.

Overall, we have standardised all holes to be M3 sized, so different components, including the baseplate, upper plate, and PCB, can be connected via M3 standoffs. This allowed for flexibility in adjusting the height, and made swapping components easier.

3. Power and Sense

Power

Generally, there are 2 main voltages present on the PCB - 12V from the LiPo battery, and 5V that is stepped down from the 12V via a voltage regulator.

In greater detail:

12V LiPo battery powers:
Motor driver to supply power to the single motor
Voltage regulator that outputs 5V with a maximum sustained current of 4A Resultant 5V from voltage regulator powers:
Sensors (LiDAR and Compass)
Microcontroller (Raspberry Pi Pico)
Camera (OpenMV M7)
Servo
Motor driver signal
Encoder on the motor

Choice of LiPo batteries

LiPo
suitable voltage - closest to most common voltage used by components 18650 - 2x3.7V?
if really needed - check conversion efficiency of voltage regulator

Communication

Various sensors, and the camera, communicate with the main microcontroller, Raspberry Pi Pico, via multiple protocols.

Inputs

LiDAR: I2C
Each LiDAR is either set to a different I2C address, or run on a different I2C bus of the Pico
Camera: UART
Compass: I2C
One compass per I2C bus for failsafe

Encoder: digital HIGH/LOW signals

Outputs

Motor driver: PWM signal
Servo: A form of PWM signal, using the Arduino Servo library

Choice of Components

Microcontroller

The Raspberry Pi Pico was chosen for various reasons:

Affordability
Pico is extremely affordable, priced at 4.00 USD each, compared to alternatives like Arduino and Teensy MCUs which can cost easily upwards of tens of US dollars.
Hence, the Pico was cost-effective and aligned with our budget constraints. We aimed to strike a balance between performance and cost, and the Pico easily met our requirements without exceeding our budget.
Fast processor and Memory
Pico has a dual-core Arm Cortex-M0+ processor that runs at 133 Mhz, which is much faster than alternatives like the Arduino Nano (16 Mhz). While it is slower than the Teensy 4.0 which runs at 400 Mhz, it has two cores instead of one, allowing for multicore operations. This is not to ignore the price advantage Pico has over alternatives.
With regards to the dual core processor, we actively took advantage of it, by running the movement control code (i.e. movement motor and steering via servo) on the second core while running the main loop gathering and processing data from sensors to make movement decisions on the main core.
Variety of Protocols and GPIO Pins
GPIO pins on the Pico are multi-purpose, and each pin could be used with almost any supported protocol, including 2 x I2C buses, 2 x SPI buses, 2 UART ports, 16 x PWM channels and 3 x analog ports.
More interfaces available than alternatives such as the Arduino Nano and Such a multitude of protocols allow us to connect any peripherals such as sensors we want.
Compatibility with Arduino
We are already familiar with the Arduino ecosystem, so finding a microcontroller that is compatible with Arduino is key
Size

Despite Pico's small size, it still packs in a lot of capabilities

Distance ranging sensor - LiDAR

LiDAR was chosen instead of alternative such as ultrasonic sensor due to its accuracy. Ultrasonic sensors, from past experience, have always been very unreliable, with values jumping around frequently, or even the entire sensor malfunctioning and causing the entire I2C bus to hang.

Besides, ultrasonic sensors may not work as well as LiDAR in this game field, where long distance ranging is required, and the field is huge (3m by 3m). Ultrasonic sensors also tend to interfere with each other, especially when we multiple need to be used simultaneously like in our case.

While the LiDAR readings may not be entirely foolproof, and are still subject to the reflectivity of the target object, they will suffice for our use.

Additionally, we had LiDAR sensors available on hand, and we have prior experience working with them, so it was a natural choice.

Initially, we were only intending on using 3 LiDARs - 2 facing left and right, and one facing forward - however we had issues with detecting corners and decided to install another pair of side facing LiDARs towards the rear. By comparing the reading from the 2 LiDARs, we were able to determine when a corner occured as the first LiDAR would no longer be detecting the wall while the rear LiDAR still was, fixing the corner detection issue.

The TFLunas used have a maximum range of 2m which is sufficient for detecting the side walls but may at times not have enough especially for the front facing LiDAR.

Battery

The vehicle is powered off a single 3-cell Lithium Polymer (LiPo) battery, which allows for high peak current draw in excess of 10A.

While we considered using 18650 batteries, since 12V was unnecessary, we ultimately decided against it.

We invested in a carrier board while testing the 18650s but it increased the footprint of the batteries and lacked the convenience of a simple XT60 connector, making swapping batteries harder. On top of that, the 2A overcurrent protection severely limited the hardware we could use.

On the other hand, we had many LiPos, was capable of handling plenty of current, and were rectangular, which made designing the bot around them much easier.

Camera

After some initial research, we shortlisted 3 main choices for a camera.

1. PixyCam
2. Raspberry Pi Camera with OpenCV
3. OpenMV

PixyCam

We had used PixyCams before but did not enjoy the lack of ability to write your own image processing algorithms. Sometimes the inbuilt algorithm simply could not recognise the colour you pick out via the UI, and you cannot do anything about it but to try and select the colour again.

Hence, we eliminated the PixyCam as a possibility.

Raspberry Pi Camera

We also considered using a Raspberry Pi Camera Module, but after some trial and error, our inexperience with writing code in OpenCV, as well as the difficulties in setting up a fully functional OpenCV environment on a full-fledged Linux distribution led us to our final decision against using it.

OpenMV

Finally, we arrived at our choice - the OpenMV M7. We had several of them on hand, and could start testing it immediately.

Compared to the power-hungry OpenCV, OpenMV is highly optimised for efficiency, thus reducing latency which is key in robotics competitions. Besides, OpenMV is tightly integrated with the OpenMV camera hardware, and provides a simplified interface in the form of the OpenMV IDE, which was way easier to use than setting up OpenCV from scratch on the Raspberry Pi.

We eventually settled on mounting an OpenMV M7 on the front of the vehicle, pointing slightly downwards to increase the field of view below the camera.

On a side note, we did consider dual/stereo cameras, and try out Simultaneous Localisation and Mapping (SLAM), but eventually decided not to due to its complexity.

PCB

While prototyping, we realised that we require the use of many sensors. We initially used bread boards to connect the microcontroller to the peripherals. We realised that connecting them via jumper wires would not be reliable. An alternative was to solder by hand using protoboards, but that would take too much time.

In the end, we decided to design and make a PCB, since manufacturing nowadays, with JLCPCB available, was cheap and quick.

Here are some renders of the PCB.

Front:


Back:


B

elo

w is

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
B. (

A

f

ull im

a

g

e is

a

v

aila

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
schemes/

)


4. Obstacle management

Open Challenge


1. For the open round, the vehicle attempts to maintain a fixed distance from the inner wall. 2 LiDARs, mounted at the front and rear of the vehicle, face the inner wall and are used to gauge the vehicle's proximity and angle with respect to the wall. Corners are detected based on the disparity between the 2 LiDAR readings with the LiDARs, with the forward LiDARs detecting the sudden increase in range before the rear LiDARs.
2. When the vehicle is started, it measures the range to the front and sides to get its start position, which is used to determine its starting section.

Obstacle Challenge


1. For the obstacle round, blocks were detected using the blob identification library that came with the OpenMV software.

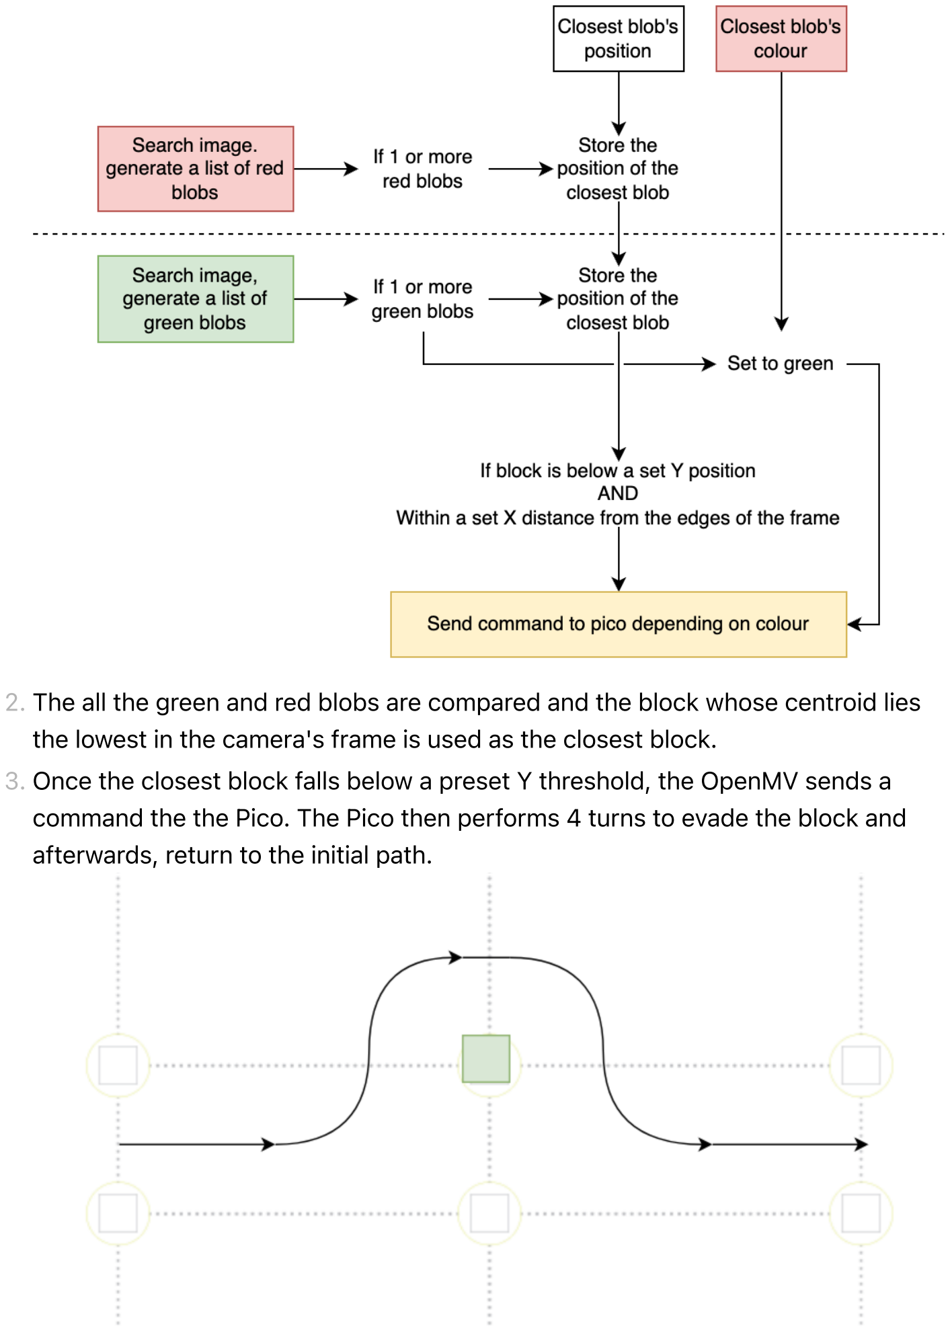
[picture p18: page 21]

2. The all the green and red blobs are compared and the block whose centroid lies the lowest in the camera's frame is used as the closest block.
3. Once the closest block falls below a preset Y threshold, the OpenMV sends a command the the Pico. The Pico then performs 4 turns to evade the block and afterwards, return to the initial path.

5. Code Style Guidelines

From the beginning, we decided to come up with a set of code style guidelines to follow, so as to help maintain consistency in our code, and to ensure the code is readable and maintainable, which is especially important as we work on complex autonomous robot systems.

The guidelines are:

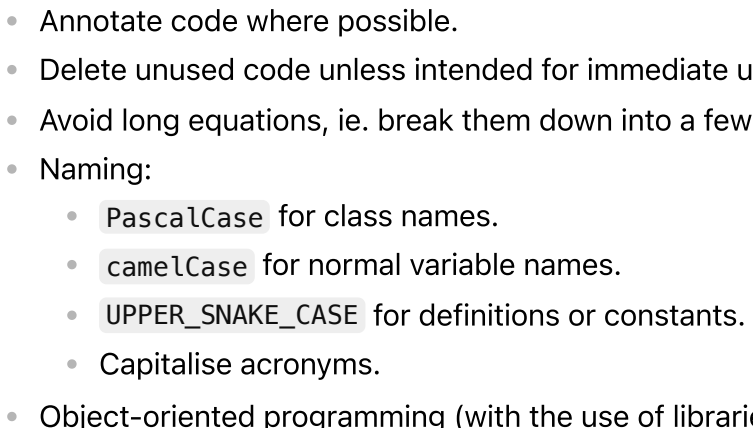
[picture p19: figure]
Annotate code where possible.; Naming: PascalCase for class names. camelCase for normal variable names. UPPER_SNAKE_CASE for definitions or constants. Capitalise acronyms.

Delete unused code unless intended for immediate use.
Avoid long equations, ie. break them down into a few statements.

Object-oriented programming (with the use of libraries and classes)

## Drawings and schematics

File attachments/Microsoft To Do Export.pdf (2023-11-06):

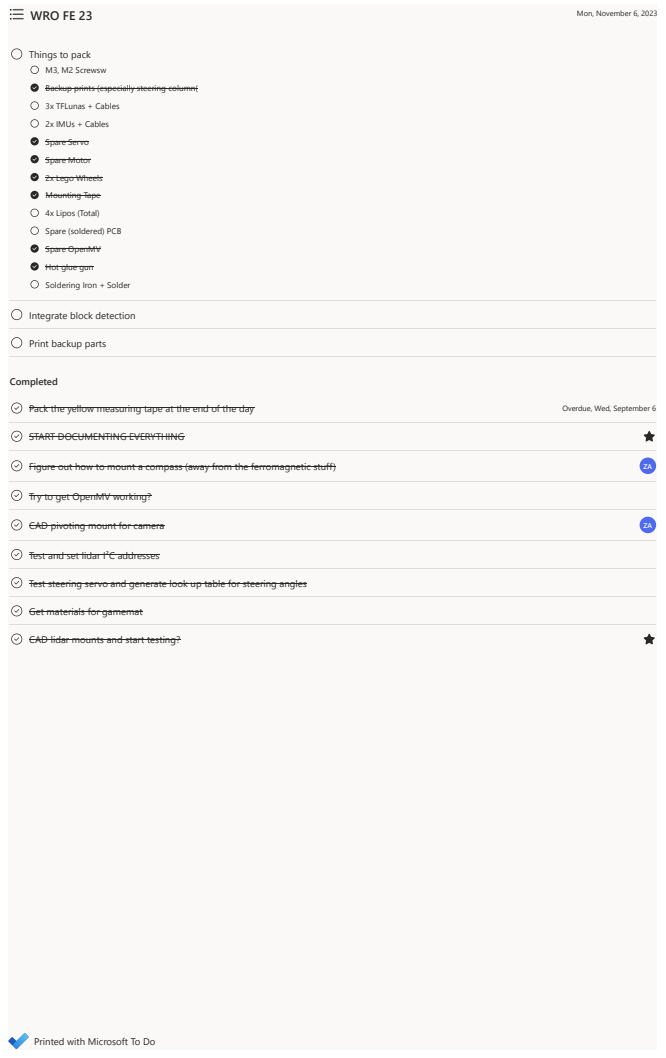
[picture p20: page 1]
Completed; WRO FE 23; Mon, November 6, 2023; Pack the yellow measuring tape at the end of the day; Overdue, Wed, September 6; Figure out how to mount a compass (away from the ferromagnetic stuff); CAD pivoting mount for camera

Things to pack
M3, M2 Screwsw
Backup prints (especially steering column(
3x TFLunas + Cables
2x IMUs + Cables
Spare Servo
Spare Motor
2x Lego Wheels
Mounting Tape
4x Lipos (Total)
Spare (soldered) PCB
Spare OpenMV
Hot glue gun
Soldering Iron + Solder

Integrate block detection

Print backup parts

START DOCUMENTING EVERYTHING

Try to get OpenMV working?

Test and set lidar I²C addresses

Test steering servo and generate look up table for steering angles

Get materials for gamemat

CAD lidar mounts and start testing?

Printed with Microsoft To Do

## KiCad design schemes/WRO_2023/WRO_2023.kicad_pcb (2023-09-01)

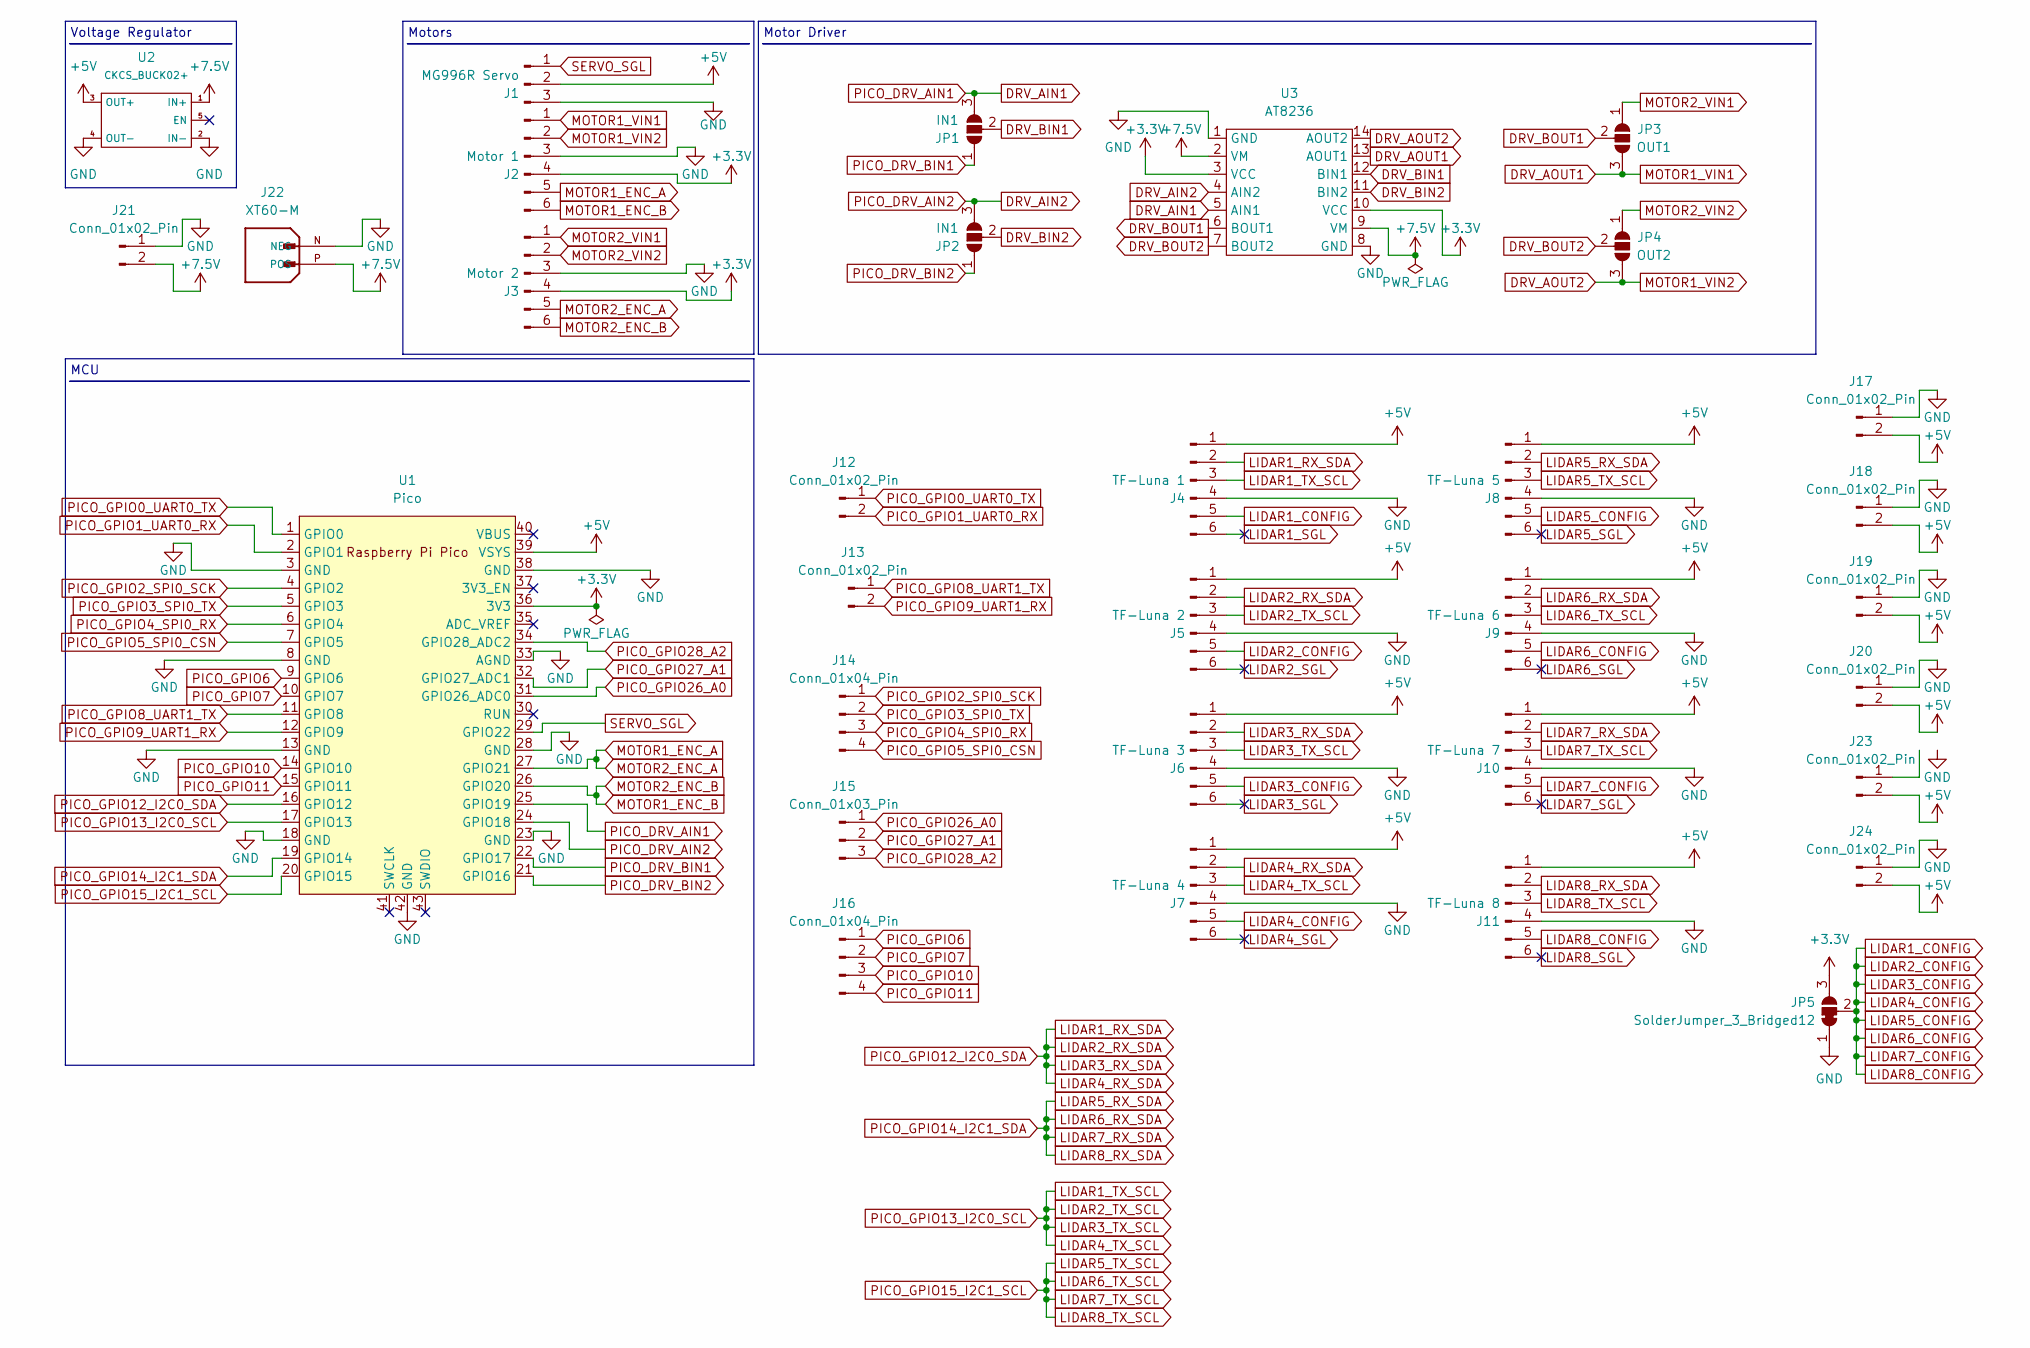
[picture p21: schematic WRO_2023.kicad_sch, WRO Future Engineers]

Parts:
J1: MG996R Servo; PinHeader_1x03_P2.54mm_Vertical
J2: Motor 1; PinHeader_1x06_P2.54mm_Vertical
J3: Motor 2; PinHeader_1x06_P2.54mm_Vertical
J4: TF-Luna 1; JST_XH_B6B-XH-A_1x06_P2.50mm_Vertical
J5: TF-Luna 2; JST_XH_B6B-XH-A_1x06_P2.50mm_Vertical
J6: TF-Luna 3; JST_XH_B6B-XH-A_1x06_P2.50mm_Vertical
J7: TF-Luna 4; JST_XH_B6B-XH-A_1x06_P2.50mm_Vertical
J8: TF-Luna 5; JST_XH_B6B-XH-A_1x06_P2.50mm_Vertical
J9: TF-Luna 6; JST_XH_B6B-XH-A_1x06_P2.50mm_Vertical
J10: TF-Luna 7; JST_XH_B6B-XH-A_1x06_P2.50mm_Vertical
J11: TF-Luna 8; JST_XH_B6B-XH-A_1x06_P2.50mm_Vertical
J12, J13, J17, J18, J19, J20, J21, J23, J24: Conn_01x02_Pin; JST_XH_B2B-XH-A_1x02_P2.50mm_Vertical
J14, J16: Conn_01x04_Pin; JST_XH_B4B-XH-A_1x04_P2.50mm_Vertical
J15: Conn_01x03_Pin; PinHeader_1x03_P2.54mm_Vertical
J22: XT60-M; AMASS_XT60-M; PARTREV V1.2
JP1, JP2: IN1; SolderJumper-3_P2.0mm_Open_TrianglePad1.0x1.5mm
JP3: OUT1; SolderJumper-3_P2.0mm_Open_TrianglePad1.0x1.5mm
JP4: OUT2; SolderJumper-3_P2.0mm_Open_TrianglePad1.0x1.5mm
JP5: SolderJumper_3_Bridged12; SolderJumper-3_P1.3mm_Bridged12_RoundedPad1.0x1.5mm
U1: Pico; RPi_Pico_SMD_TH
U2: CKCS_BUCK02+
U3: AT8236

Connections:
+3.3V: J2.4, J3.4, JP5.3 (B), U1.36 (3V3), U3.3 (VCC), U3.10 (VCC)
+5V: J1.2, J4.1, J5.1, J6.1, J7.1, J8.1, J9.1, J10.1, J11.1, J17.2, J18.2, J19.2, J20.2, J23.2, J24.2, U1.39 (VSYS), U2.3 (OUT+)
+7.5V: J21.2, J22.P (POS), U2.1 (IN+), U3.2 (VM), U3.9 (VM)
DRV_AIN1: JP1.3 (B), U1.25 (GPIO19), U3.5 (AIN1)
DRV_AIN2: JP2.3 (B), U1.24 (GPIO18), U3.4 (AIN2)
DRV_AOUT1: J2.1, JP3.3 (B), U3.13 (AOUT1)
DRV_AOUT2: J2.2, JP4.3 (B), U3.14 (AOUT2)
DRV_BIN1: JP1.2 (C), U3.12 (BIN1)
DRV_BIN2: JP2.2 (C), U3.11 (BIN2)
DRV_BOUT1: JP3.2 (C), U3.6 (BOUT1)
DRV_BOUT2: JP4.2 (C), U3.7 (BOUT2)
GND: J1.3, J2.3, J3.3, J4.4, J5.4, J6.4, J7.4, J8.4, J9.4, J10.4, J11.4, J17.1, J18.1, J19.1, J20.1, J21.1, J22.N (NEG), J24.1, JP5.1 (A), U1.3 (GND), U1.8 (GND), U1.13 (GND), U1.18 (GND), U1.23 (GND), U1.28 (GND), U1.33 (AGND), U1.38 (GND), U1.42 (GND), U2.2 (IN-), U2.4 (OUT-), U3.1 (GND), U3.8 (GND)
LIDAR1_CONFIG: J4.5, J5.5, J6.5, J7.5, J8.5, J9.5, J10.5, J11.5, JP5.2 (C)
LIDAR1_RX_SDA: J4.2, J5.2, J6.2, J7.2, U1.16 (GPIO12)
LIDAR1_SGL: J4.6
LIDAR1_TX_SCL: J4.3, J5.3, J6.3, J7.3, U1.17 (GPIO13)
LIDAR2_SGL: J5.6
LIDAR3_SGL: J6.6
LIDAR4_SGL: J7.6
LIDAR5_RX_SDA: J8.2, J9.2, J10.2, J11.2, U1.19 (GPIO14)
LIDAR5_SGL: J8.6
LIDAR5_TX_SCL: J8.3, J9.3, J10.3, J11.3, U1.20 (GPIO15)
LIDAR6_SGL: J9.6
LIDAR7_SGL: J10.6
LIDAR8_SGL: J11.6
MOTOR1_ENC_A: J2.5, J3.5, U1.27 (GPIO21)
MOTOR1_ENC_B: J2.6, J3.6, U1.26 (GPIO20)
MOTOR2_VIN1: J3.1, JP3.1 (A)
MOTOR2_VIN2: J3.2, JP4.1 (A)
PICO_DRV_BIN1: JP1.1 (A), U1.22 (GPIO17)
PICO_DRV_BIN2: JP2.1 (A), U1.21 (GPIO16)
PICO_GPIO0_UART0_TX: J12.1, U1.1 (GPIO0)
PICO_GPIO1_UART0_RX: J12.2, U1.2 (GPIO1)
PICO_GPIO2_SPI0_SCK: J14.1, U1.4 (GPIO2)
PICO_GPIO3_SPI0_TX: J14.2, U1.5 (GPIO3)
PICO_GPIO4_SPI0_RX: J14.3, U1.6 (GPIO4)
PICO_GPIO5_SPI0_CSN: J14.4, U1.7 (GPIO5)
PICO_GPIO6: J16.1, U1.9 (GPIO6)
PICO_GPIO7: J16.2, U1.10 (GPIO7)
PICO_GPIO8_UART1_TX: J13.1, U1.11 (GPIO8)
PICO_GPIO9_UART1_RX: J13.2, U1.12 (GPIO9)
PICO_GPIO10: J16.3, U1.14 (GPIO10)
PICO_GPIO11: J16.4, U1.15 (GPIO11)
PICO_GPIO26_A0: J15.1, U1.31 (GPIO26_ADC0)
PICO_GPIO27_A1: J15.2, U1.32 (GPIO27_ADC1)
PICO_GPIO28_A2: J15.3, U1.34 (GPIO28_ADC2)
SERVO_SGL: J1.1, U1.29 (GPIO22)

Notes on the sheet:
Voltage Regulator
Motor Driver
MCU
Motors

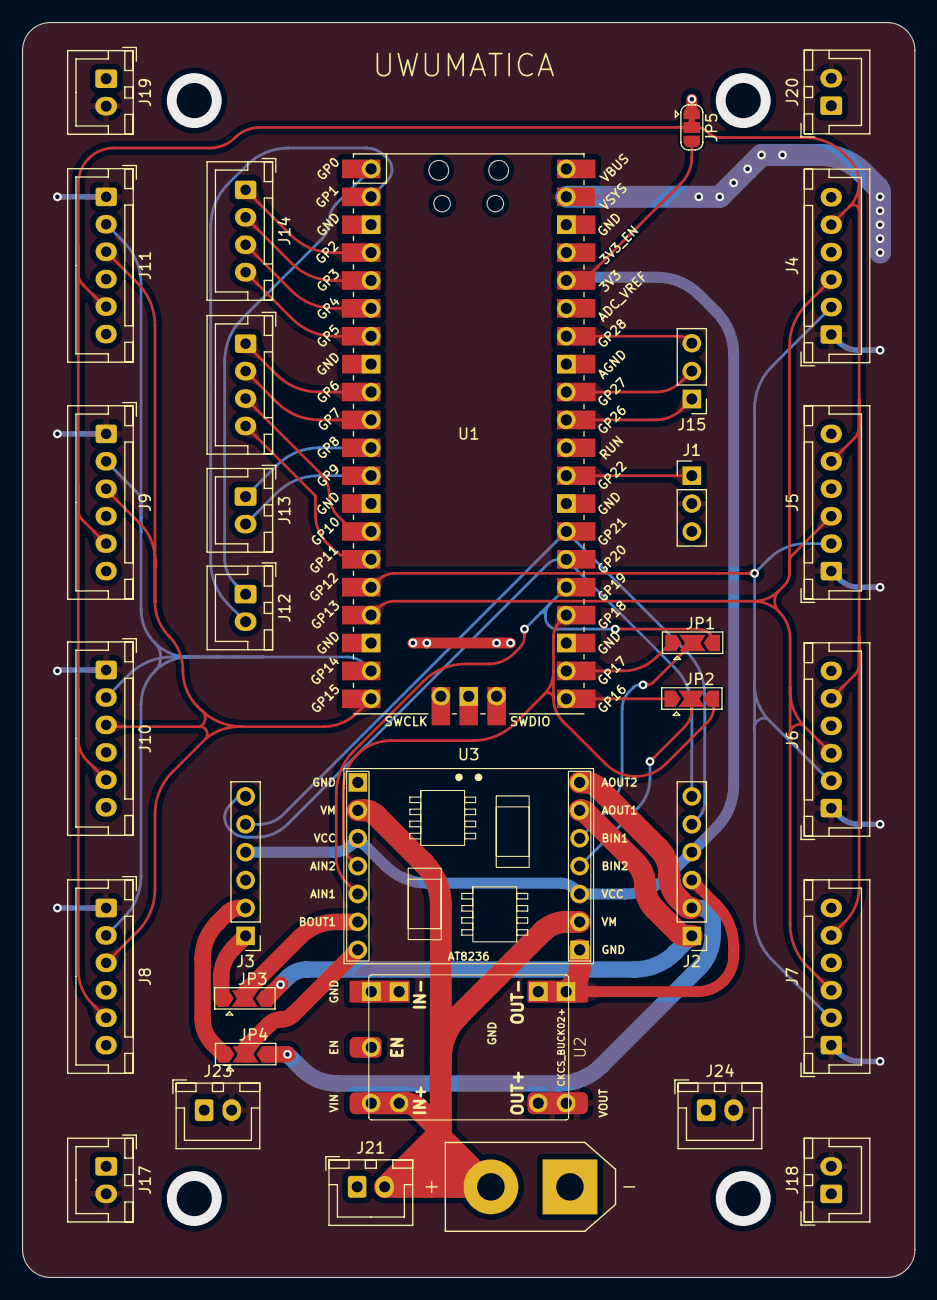
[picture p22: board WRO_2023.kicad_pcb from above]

Board: 2 copper layers, 81.3 x 114.3 mm, 32 parts (0 on the bottom side), 39 nets.

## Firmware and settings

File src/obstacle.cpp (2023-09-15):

#include <Common.h>

#define SPEED 0.5
#define MIN_TURN_RATIO 0.2f
#define MAX_CORNER_COUNT 12
#define TURN_ANGLE 70
#define MOVE_DISTANCE 15
#define TURNING_RADIUS 15
#define ROBOT_WIDTH 20
// #define MIN_ERROR 1
#define MIN_WALL_DISTANCE 43
#define MIN_ERROR 1
#define MIN_RESPONSE_ANGLE 30
#define POWER 0.4

void changeL(bool isLeft = true) {
    int dir = isLeft ? -1 : 1;

    turn2(currentSide * 90 + TURN_ANGLE * dir, 0, true, MIN_ERROR, MIN_TURN_RATIO, SPEED, MIN_RESPONSE_ANGLE, POWER);
    // moveStraight(5);
    turn2(currentSide * 90 , 0, true, MIN_ERROR, MIN_TURN_RATIO, SPEED, MIN_RESPONSE_ANGLE, POWER); // face straight
    moveStraight(5, true);
    turn2(currentSide * 90 - TURN_ANGLE * dir, 0, true, MIN_ERROR, MIN_TURN_RATIO, SPEED, MIN_RESPONSE_ANGLE, POWER);
    // moveStraight(5);
    turn2(currentSide * 90, 0, true, MIN_ERROR, MIN_TURN_RATIO, SPEED, MIN_RESPONSE_ANGLE, POWER); // face straight
}

void loop() {
    start:
        speed = 0;
        turnRatio = 0;
        currentCase = 0;
        if (button.isPressed()) {
            trueAngleZeroError = 0;
            delay(100);
            trueAngleZeroTare(trueAngle);
            
            // FOR DEBUG/TUNING
            // turn2(90, 0, true, MIN_ERROR, MIN_TURN_RATIO, SPEED, MIN_RESPONSE_ANGLE, POWER); // face straight
            // changeL(false);
            // return;
            
            goto initial_lane;
        } else {
            goto start;
        }

    initial_lane: // first straight lane - 2 possibilities: no block, turn immediately, or with block, avoid and turn after block
        currentCase = 1;

        trueAngleZeroTare(trueAngle);
        initialDistLeft = distLeft;
        initialDistRight = distRight;
        initialDistFront = distFront;

        speed = SPEED;

        justTurned = true;

        goto move_straight;

    corner_turn:
        currentCase = 2;

        if (cornerCount == 0) {
            isClockwise = distLeftCorr - distRightCorr < 0;
            initialInnerDist = isClockwise ? initialDistRight : initialDistLeft;
            initialOuterDist = isClockwise ? initialDistLeft : initialDistRight;
        }
        
        cornerCount++;

        while (distFront > 20 + TURNING_RADIUS) {
            correctToRelativeZero();
        }

        // faceStraight();

        currentSide = POS_MOD(currentSide + (isClockwise ? 1 : -1), 4);
        turn2(currentSide * 90, isClockwise ? -1 : 1, true, MIN_ERROR, MIN_TURN_RATIO, SPEED, MIN_RESPONSE_ANGLE, POWER);

        // goto start;

        // if (cornerCount >= MAX_CORNER_COUNT) {
        //     goto finish; // END
        // } else {
        //     justTurned = true;
        //     goto move_straight; // wall detected, change state
        // }

        justTurned = true;
        goto move_straight;

    move_straight:
        currentCase = 3;

        if (justTurned) {
            justTurned = false;
            while (abs(headingDiff) > 45 || innerDist > 100 || innerDistBack > 100) { // move straight until wall detected
                correctToRelativeZero();

                if (isCameraPresent) {
                    goto avoid_block;
                }
            }
        }

        while (headingDiff < 45) { // wall track until corner or block 
            if (cornerCount >= MAX_CORNER_COUNT) {
                float initialDistance = encoderDistance;
                float targetDistance = distFront - initialDistFront;
                if (distFrontCorr - initialDistFront < 5 && (encoderDistance - initialDistance) > targetDistance) break;
            }

            if (cornerCount == 0) { // first lane, dunno clockwise or anticlockwise
                if (abs(distLeft - distRight) > 100) break;
            } else {
                if (innerDist > 100) break;
            }
            EPRINT(headingDiff)
            EPRINT(innerDist)

            if (isCameraPresent) {
                goto avoid_block;
            }

            if (abs(innerDistCorr - MIN_WALL_DISTANCE) <= 3) { // move straight
                correctToRelativeZero();
            } else {
                float distToCorrectTo = (outerDistCorr + outerDistBackCorr) / 2;
                // correctToWall(MIN_WALL_DISTANCE, 30, distToCorrectTo);
                correctToWall(MIN_WALL_DISTANCE, 30);
            }
            // correctToRelativeZero();
        }

        if (cornerCount >= MAX_CORNER_COUNT) {
            goto finish; // END
        } else {
            goto corner_turn; // wall missing, change state
        }

        // goto corner_turn; // wall missing, change state

    avoid_block:
        currentCase = 4;

        if (isBlockRed) {
            changeL(false);
            // changeL(true);
        } else {
            changeL(true);
            // changeL(false);
        }
        goto move_straight;

    finish:
        currentCase = 5;

        // faceStraight();

        // while (abs(headingDiff) > 45 || innerDist > 100 || innerDistBack > 100) { // move straight until wall detected
        //     correctToRelativeZero();
        // }

        // float initialDistance = encoderDistance;
        // float targetDistance = distFront - initialDistFront;
        // while (distFrontCorr - initialDistFront > 5 || encoderDistance - initialDistance < targetDistance - 5) {
        //     correctToWall(initialInnerDist);
        // }

        // reset variables
        speed = 0;
        turnRatio = 0;
        cornerCount = 0;
        currentSide = 0;
        trueAngleZeroError = 0; // hacks :D - trueAngleTare relies on trueAngle instead of imu.readAngle (cannot be used on main core)
        isClockwise = false;

        goto start;
}

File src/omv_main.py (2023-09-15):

# Multi Color Blob Tracking Example
#
# This example shows off multi color blob tracking using the OpenMV Cam.
import sensor, image, time, math, pyb, struct
from pyb import UART
uart = UART(1, 9600)
uart.init(9600, bits=8, parity=None, stop=1, timeout_char=1000)
# Color Tracking Thresholds (L Min, L Max, A Min, A Max, B Min, B Max)
# The below thresholds track in general red/green things. You may wish to tune them...
#redThreshold = [(15, 55, 13, 65, -3, 47)]
#redThreshold = [(13, 82, -16, 65, 9, 57)]
#redThreshold = [(6, 36, 6, 46, 3, 19)]
redThreshold = [(6, 34, 6, 26, 3, 16)]
#redThreshold = [(6, 29, 6, 46, 3, 16)]
# greenThreshold = [(0, 100, -29, -9, 9, 32)]
# greenThreshold = [(0, 100, -29, -4, 6, 47)]
# greenThreshold = [(20, 60, -45, -5, 4, 38)]
# greenThreshold = [(20, 60, -60, 5, 5, 50)]
#greenThreshold = [(20, 60, -60, -5, 5, 50)]
#greenThreshold = [(20, 60, -60, -10, 5, 50)]
greenThreshold = [(16, 40, -35, -8, -3, 25)]

# You may pass up to 16 thresholds above. However, it's not really possible to segment any
# scene with 16 thresholds before color thresholds start to overlap heavily.

#EDGE_THRESHOLD = 40 # 80, 40, 20
EDGE_THRESHOLD=80
TURN_TRIGGER_DISTANCE = 40   # 80, 40, 20
OFFSET_MULTIPLIER = 0.4

sensor.reset()
sensor.set_pixformat(sensor.RGB565)
sensor.set_framesize(sensor.QQVGA)
#sensor.set_framerate()
sensor.skip_frames(time = 2000)
sensor.set_auto_gain(False, gain_db = 2.7661) # must be turned off for color tracking
sensor.set_auto_whitebal(False, (-6.02073, -3.25462, 1.88336)) # must be turned off for color tracking
sensor.set_saturation(-2)
sensor.set_framebuffers(1)
sensor.set_vflip(True)

LEDred = pyb.LED(1)
LEDgreen = pyb.LED(2)
LEDblue = pyb.LED(3)

def LEDwhite():
    LEDred.on()
    LEDgreen.on()
    LEDblue.on()

def LEDoff():
    LEDred.off()
    LEDgreen.off()
    LEDblue.off()

LEDoff()
LEDwhite()

clock = time.clock()

# Only blobs that with more pixels than "pixel_threshold" and more area than "area_threshold" are
# returned by "find_blobs" below. Change "pixels_threshold" and "area_threshold" if you change the
# camera resolution. Don't set "merge=True" becuase that will merge blobs which we don't want here.

# left region of interest
lROI = (0, TURN_TRIGGER_DISTANCE, EDGE_THRESHOLD, 240 - TURN_TRIGGER_DISTANCE)
rROI = (320-EDGE_THRESHOLD, TURN_TRIGGER_DISTANCE, EDGE_THRESHOLD, 240 - TURN_TRIGGER_DISTANCE)

isTakePhoto = False
lastPhotoTaken = time.time_ns()
TIME_INTERVAL = 2

while(True):
#    print(sensor.get_rgb_gain_db())
    clock.tick()
    img = sensor.snapshot()
    img.lens_corr(1.65)
    if (isTakePhoto):
        if ((time.time_ns() - lastPhotoTaken) > TIME_INTERVAL*1000*1000000):
            lastPhotoTaken = time.time_ns()
            img.save(str(lastPhotoTaken))
            print("Taken!")
            LEDwhite()
        else:
            LEDoff()
        continue

    redBlobs = []
    greenBlobs = []
    closestBlobIsRed = True
    width = img.width()
    height = img.height()
    closestBlob = [int(width/2), 0] # could potentially compare by size (due to image bug, but defeats purpose)

#    for blob in img.find_blobs(redThreshold, roi=lROI):
#        print(blob)
#    for blob in img.find_blobs(redThreshold, roi=rROI):
#        print(blob)

    for blob in img.find_blobs(redThreshold, pixels_threshold=200, area_threshold=200):
        if blob.cy() > closestBlob[1]:
            closestBlob = [blob[5], blob[6]]

    for blob in img.find_blobs(greenThreshold, pixels_threshold=200, area_threshold=200):
        if blob.cy() > closestBlob[1]:
            closestBlob = [blob[5], blob[6]]
            closestBlobIsRed = False

#    img.binary(redThreshold)
#    for l in img.find_lines(threshold = 10000, theta_margin = 10, rho_margin = 10):
##        if (0 <= l.theta()) and (l.theta() <= 179):
#        img.draw_line(l.line(), color = (255, 0, 0))
#            # print(l)

#    offset = (-1 if closestBlobIsRed else 1) * OFFSET_MULTIPLIER * closestBlob[1]

    print(closestBlob)
    # LEDwhite()
    if (closestBlob[0] < EDGE_THRESHOLD or closestBlob[0] > width-EDGE_THRESHOLD) : # x value
        if closestBlob[1] > TURN_TRIGGER_DISTANCE: # y value
            if closestBlobIsRed:
                command = 1
                LEDred.on()
            else:
                command = 0
                LEDgreen.on()
            if closestBlob[0] < 0.5 * width: # if on the right
                command + 2
                # LEDblue.on()
            print(command)
            uart.writechar(command)
        else:
            LEDoff()
            # LEDwhite()
    else:
        LEDoff()
        LEDwhite()
#    img.draw_rectangle(lROI)
#    img.draw_rectangle(rROI)

    img.draw_line(EDGE_THRESHOLD, 0, EDGE_THRESHOLD, height)
    img.draw_line(width - EDGE_THRESHOLD, 0, width - EDGE_THRESHOLD, height)
    img.draw_line(0, TURN_TRIGGER_DISTANCE, width, TURN_TRIGGER_DISTANCE)
    img.draw_cross(closestBlob[0], closestBlob[1])

    #img.draw_arrow(int(width/2), closestBlob[1],closestBlob[0] + offset , closestBlob[1])

#    deviation = (closestBlob[0] + offset)/width
#    deviation = max(0, min(1, deviation))
#     # converting to a 8 bit value
#    print(struct.pack("<B", int(deviation * 255)))
    #uart.write(bin(deviation))

    if uart.any():
        print(uart.read())

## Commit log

2023-05-23 feat: Add I2C scanner
2023-06-19 feat: Add pico test file
2023-06-19 platformio: fix: Add I2C scanner config
2023-06-20 test: feat: Add LED blink
2023-07-14 test: feat: Add servo test code
2023-07-17 feat: Add motor test code for 2 different drivers
2023-07-17 test: feat: Add encoder test code
2023-07-24 test: feat: Add motor encoder test for protoboard
2023-07-27 feat(lib): Add Lidar library
2023-07-27 feat: Automate scanning both I2C bus for I2C scanner
2023-08-01 feat: Add init for LED pin by setting pinMode
2023-08-04 feat(lib): Add encoder library
2023-08-04 feat(test): Add test code for encoder library
2023-08-04 feat(lib): Add Motor library
2023-08-04 feat(test): Add test code for Motor library
2023-08-04 feat(lib): Add Button library
2023-08-04 feat(test): Add test code for Button library
2023-08-04 feat: Add button pins to Definitions.h
2023-08-04 refactor(test): Use defined macro instead of pin integers
2023-08-04 feat: Add wheel diameter to Definitions.h
2023-08-04 feat(test): Add test code for motor and encoder combined
2023-08-04 feat: Add IMU calibration code
2023-08-04 feat(test): Add Lidar library test code
2023-08-11 chore: Remove debug print
2023-08-11 feat(test): Add different kinds of servo movements
2023-08-16 test: feat: Use interrupts when checking encoder
2023-08-16 chore: Updated IMU calibration
2023-08-16 feat: Update main code with new encoder and turning
2023-08-18 ci: fix: Remove extra wrong character
    [pico_lib_driveservo.cpp]
2023-08-18 chore: Update IMU calibration values
2023-08-24 feat: Add minimal interval between button presses
2023-08-24 feat: Add new definition for front LiDAR spacing
2023-08-24 feat: New fixed Desmos graph for calibration, with new calibrated values
    [pico_imu_calibration.cpp]
2023-08-24 feat: Add test code for Open Challenge using only inner LiDAR
2023-08-24 feat: Add images for main colours to print
2023-08-24 !feat: Major update to code - use combination of synchronous blocking code and async state machine - rename taring functions and variables - new blocking turn function - new blocking move straight fu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
2023-08-28 feat: Update - updated IMU calibration values - reduced WALL_PRESENT_DISTANCE constant - turn on LED for blocking functions (turn and moveStraight) - fix: cos instead of sin for corrected front LiDAR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
2023-08-29 feat: Add sample code for new case
2023-08-29 feat: Add camera-based test code for open challenge
2023-08-29 feat(lib): Updated Encoder library using interrupt
2023-08-29 feat: Update main code to use new Encoder library
2023-08-29 chore: Rename images subdir to attachments
2023-08-29 fix(lib): Actually working Encoder library using interrupts
2023-08-29 chore: Update main code for use with new Encoder library
2023-08-29 feat: Updates - use old LiDAR readings if currently reading zero - define outer and inner distances globally - add direction parameter to turn function - set LiDAR FPS to 250 - remove moving forward 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
2023-08-29 feat(lib): Read high bit for LiDAR
2023-08-29 fix: Update test code using new Encoder library
    [pico_lib_motor_encoder_pcb.cpp]
2023-08-29 fix: Turn function now use tared trueAngle not the raw IMU angle
2023-08-30 feat: Add back LiDARs
2023-08-30 feat: Add Debug prints
2023-08-30 feat: General improvements to wall track - add 1ms delay in second core loop to prevent servo updates being too fast - add conditionals to restricting turns - add initial startup servo turns
2023-08-30 feat: Major updates - add lidarHeading - estimate based on diff in LiDAR readings - add headingDiff - diff in relativeAngle and LiDAR heading - relativeAngle calculation using current side instead of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
2023-08-30 feat: General improvements - cleanup code - increase speed to 0.5 - change right back LiDAR address - default clockwise - fix: Lidar-based heading when going clockwise
2023-08-30 feat: Update Common.h - update IMU calibration - add TURNING_RADIUS definition
2023-08-30 feat: Functional open challenge code - add MAX_CORNER_COUNT definition - add different move straight dependent on initial conditons for last turn - add face straight and track inner wall for last sec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
2023-08-30 chore: Update IMU calibrations
2023-08-31 fix: Update Common.h - cleanup, organise - add comments - update IMU calibration - add DIST_BETWEEN_TWO_LIDARS definition - fix!: distances using distLeft instead of correct sides - rename variables 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
2023-09-01 fix: Update IMU library with calibration fix
2023-09-01 feat: Update OpenMV code - init UART - updated trigger distance - use writechar instead of write
2023-09-01 feat: Update IMU calibration test code to include second IMU
2023-09-01 feat: Update open.cpp and Common.h For open.cpp: - refactor: Move setup, setup1 and loop1 to Common.h - chore: remove unused code - refactor: last corner move straight until align with origin positio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
2023-09-01 docs: update(): 20230901-16:02
    [bot.f3d]
2023-09-01 chore: Update IMU submodule
2023-09-01 fix: Update IMU git submodule
2023-09-01 feat: Add PCB and Schematics
    [WRO_2023.kicad_pcb, WRO_2023.kicad_sch]
2023-09-01 chore: Delete unused attachments
2023-09-01 docs: Add PCB and Schematics
2023-09-01 ci: fix: Update IMU submodule
2023-09-05 chore: Update IMU calibration
2023-09-05 !refactor: Open challenge code and Common.h - use goto instead of switch - a lot of cleanup and organisation and refactor yes.
2023-09-05 feat: Add vector resolution and summation for encoder distance
2023-09-05 !feat: Add obstacle code and update Common.h For Common.h: - do not print in first core - fix: camera buffer could be 0 to 3
    [obstacle.cpp]
2023-09-05 feat: Update OpenMV code - feat: functions for colour LEDs and call them
2023-09-13 chore: Set servo middle to 1500 for debug
2023-09-15 feat: Update OpenMV code
    - feat: Update red and green block thresholds
    - feat: Add actual fixed gain and white balance
    - fix: Set frame buffer to fix discontinued image bug
    - feat: Add taking photo mode
    [omv_main.py]
2023-09-15 feat: Update Open challenge code
    - fix: Continuously tare during start case, and add delay after button press
    - refactor: Use updated turn function
    - fix: Slow down for last corner to get accurate front LiDAR readings
    - fix: Remove faceStraight function - causing robot to not stop
    - fix: Use 100cm instead of 70cm for innerDist to prevent false trigger
    - fix: Remove encoder for last lap as it did not stop
2023-09-15 feat: Update Common.h
    - chore: Updated IMU calibration
    - feat: Add parameters to correctToRelativeZero to set a min turnRatio
    - feat: Add distance to correct to as a parameter in correctToWall
    - fix: Potential divide by zero in correctToWall
    - fix: New way to tare angle using a shared boolean
    - feat: Average IMU angle using vector resolution
    - feat: Average heading calculated from LiDAR using vector resolution
    - feat: Average outer LiDAR readings
    - feat: Add minRespondAngle and power parameters to turn function
2023-09-15 feat: Update Obstacle challenge code
    - feat: Use new turn2 function
    - fix: Continuously tare angle in start state
    - feat: Add ending condition and state - move back
    [obstacle.cpp]
